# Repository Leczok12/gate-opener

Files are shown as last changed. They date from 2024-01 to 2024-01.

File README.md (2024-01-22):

# GATE OPENER V2

## Description

This device can open gate remotly using ESP RainMaker app or Google home.

## Files

- 3D files (case for remtoe and device)
  - [device](./case/device/)
  - [remote](./case/remote/)
- Kicad files (pcb files)
  - [ready for print pdf files](./pcb/)
  - [device](./pcb/main-board/)
  - [remote](./pcb/remote-controller-board/)
- Arduino IDE files (with software)
  - [software](./software/)

## Appearance of the device

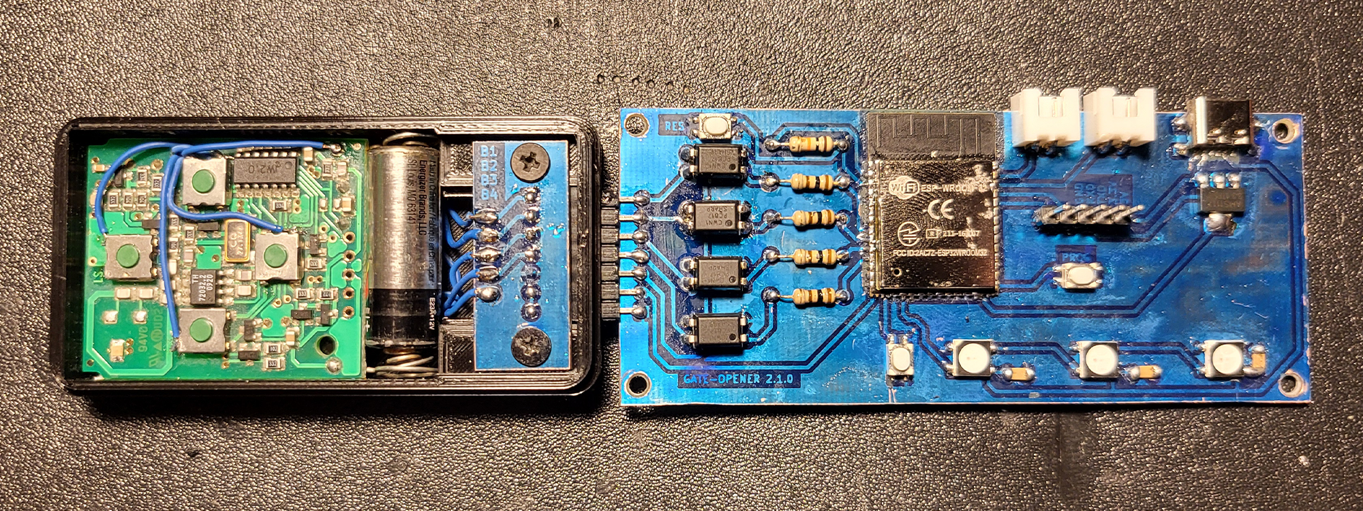
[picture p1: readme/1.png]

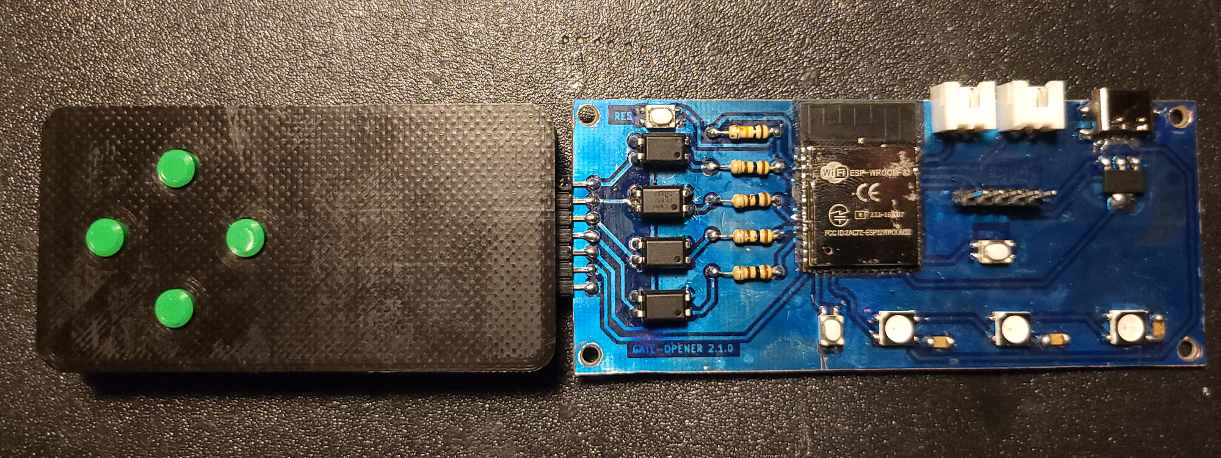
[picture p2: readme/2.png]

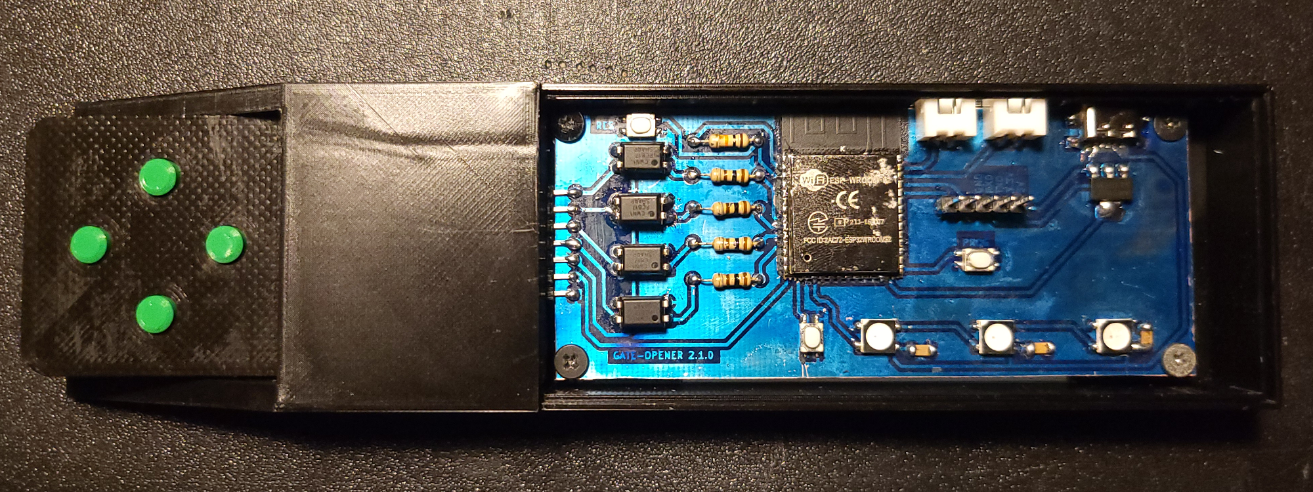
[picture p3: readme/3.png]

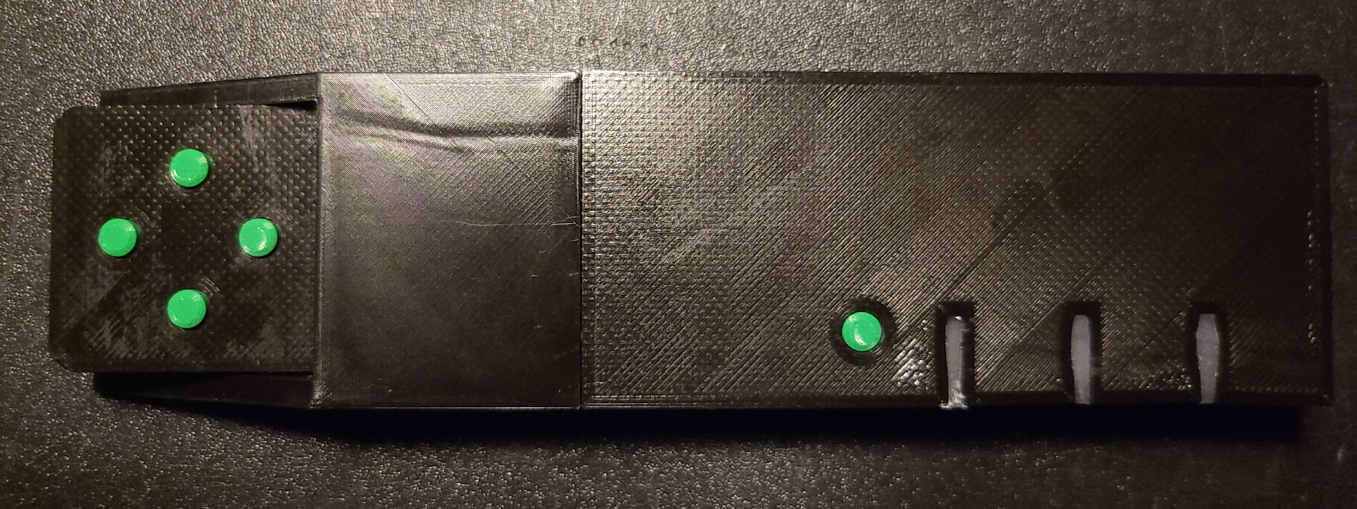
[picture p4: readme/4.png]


## Shopping list

| Name | Amount | Url |
| :---: | :----: | :--- |
| ESP-WROOM32 | 1 | [Aliexpress](https://aliexpress.com/item/32808772590.html) |
| WS2812B LED | 3 | [Aliexpress](https://aliexpress.com/item/4001345875756.html) |
| Capacitor SMD 100nf | 3 | [Aliexpress](https://aliexpress.com/item/1005002769519482.html) |
| USB-C 6 pin | 1 | [Aliexpress](https://aliexpress.com/item/32966491026.html) |
| Pin header 7 pin and 5 pin | 1 | [Aliexpress](https://aliexpress.com/item/1005005258694395.html) |
| Pin socket 7 pin | 1 | [Aliexpress](https://aliexpress.com/item/4001198421663.html) |
| Resistor 10K ohm | 1 | - |
| PC817 | 4 | - |
| Resistor 100ohm | 4 | - |
| Momentary switch 3x4x2.5mm | 3 | - |
| AMS117 3.3V | 1 | - |
| JST_XH_2.54 2 pin sockets  | 2 | - |
| gate remote\* | 1 | - |

\* in my case it is **HORMANN HSM4-868**

## Software

### Requirements

- ARDUINO IDE
  - NeoPixel
  - RainMaker

Create config.hpp file in software dir using config-template.hpp and fill gaps.

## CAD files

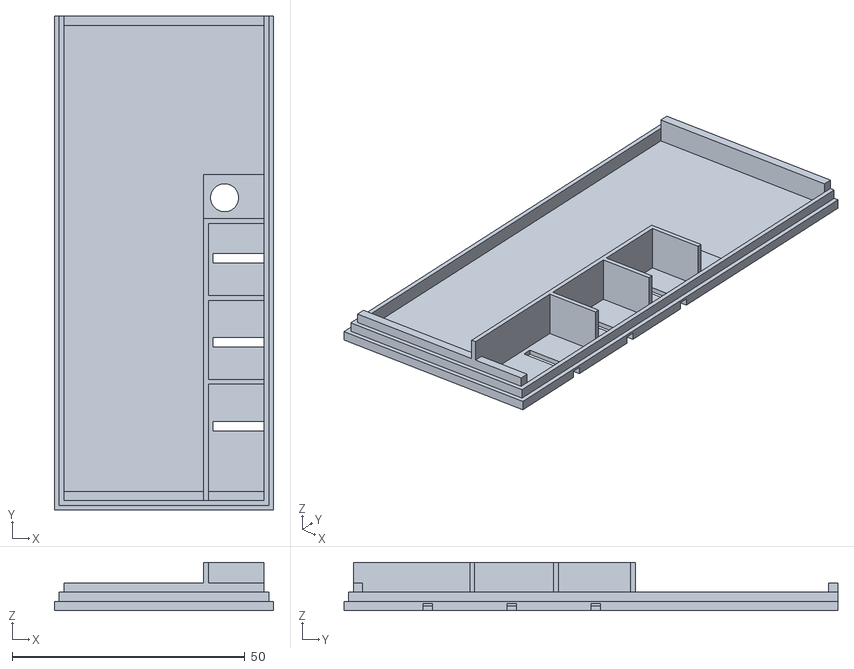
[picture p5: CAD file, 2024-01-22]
case/device/case-top.stl
47.0 x 106.0 x 10.4

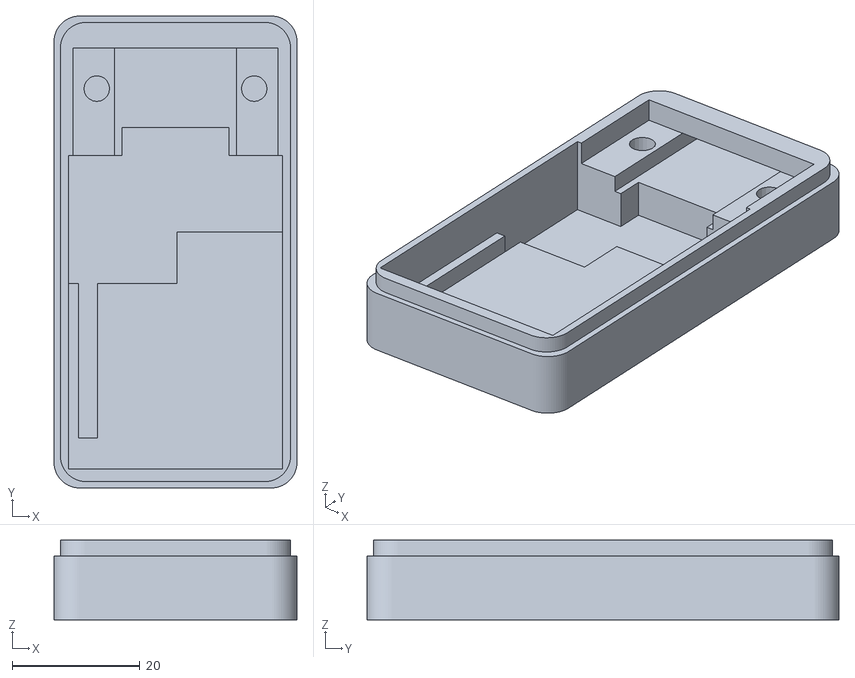
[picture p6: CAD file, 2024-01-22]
case/remote/case-bottom.stl
38.0 x 73.8 x 12.5

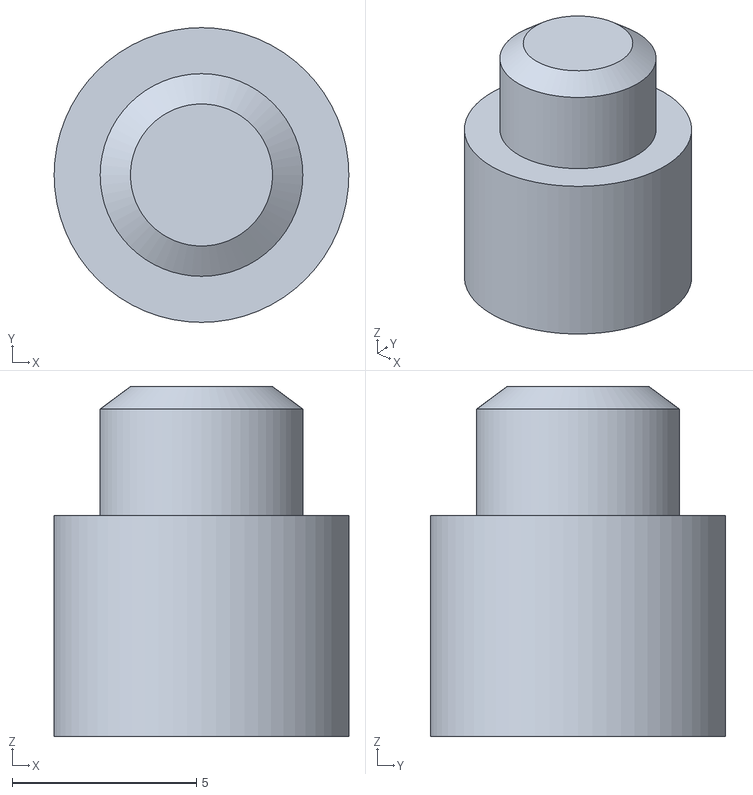
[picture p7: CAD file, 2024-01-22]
case/device/button.stl
8.00 x 8.00 x 9.50

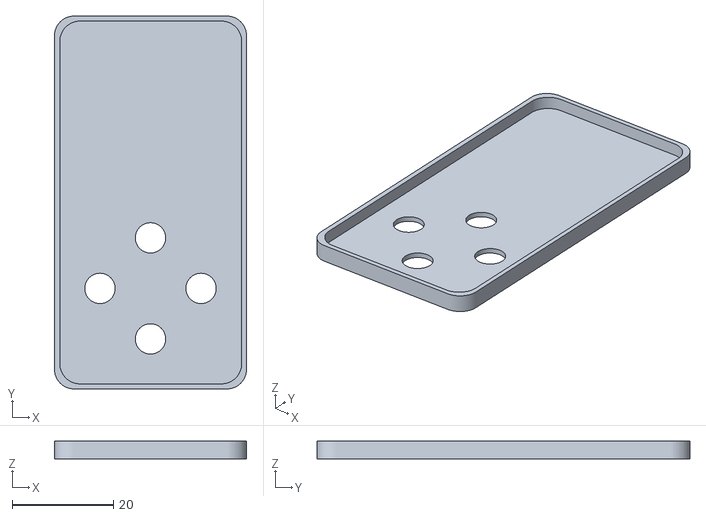
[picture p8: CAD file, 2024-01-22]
case/remote/case-top.stl
38.0 x 73.8 x 3.50

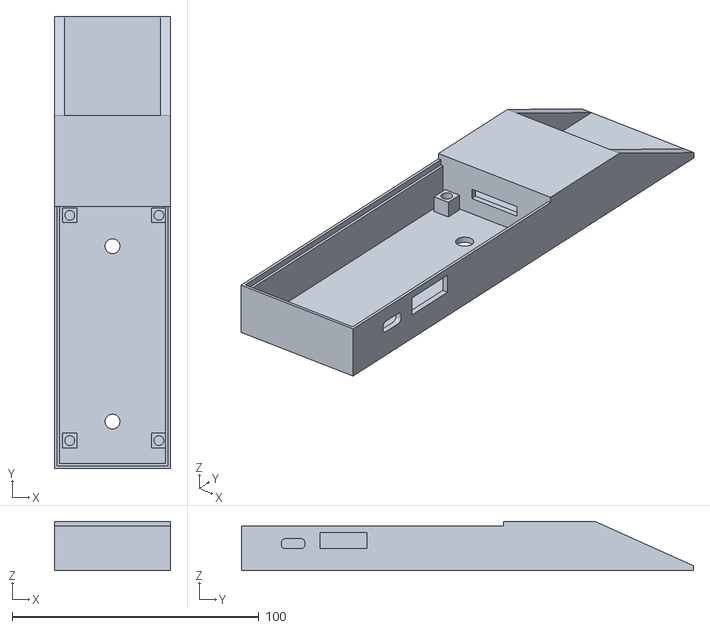
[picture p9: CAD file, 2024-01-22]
case/device/case-bottom.stl
47.0 x 183.0 x 20.0

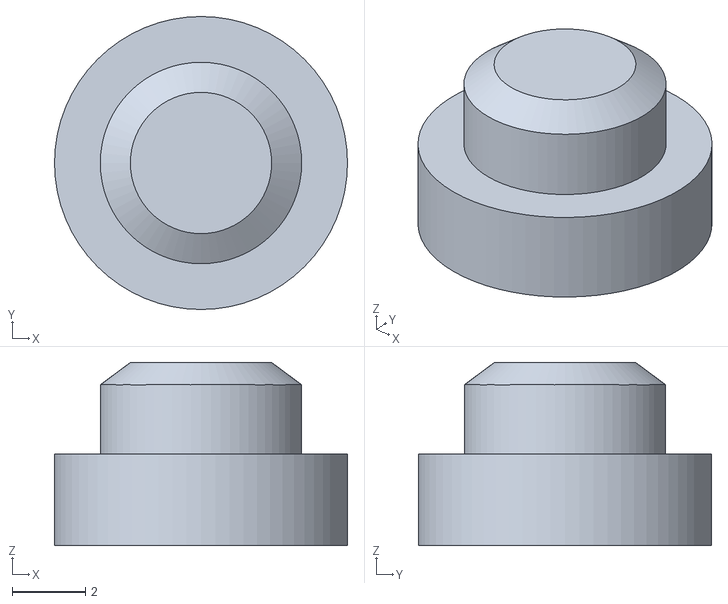
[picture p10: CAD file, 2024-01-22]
case/remote/button.stl
8.00 x 8.00 x 5.00

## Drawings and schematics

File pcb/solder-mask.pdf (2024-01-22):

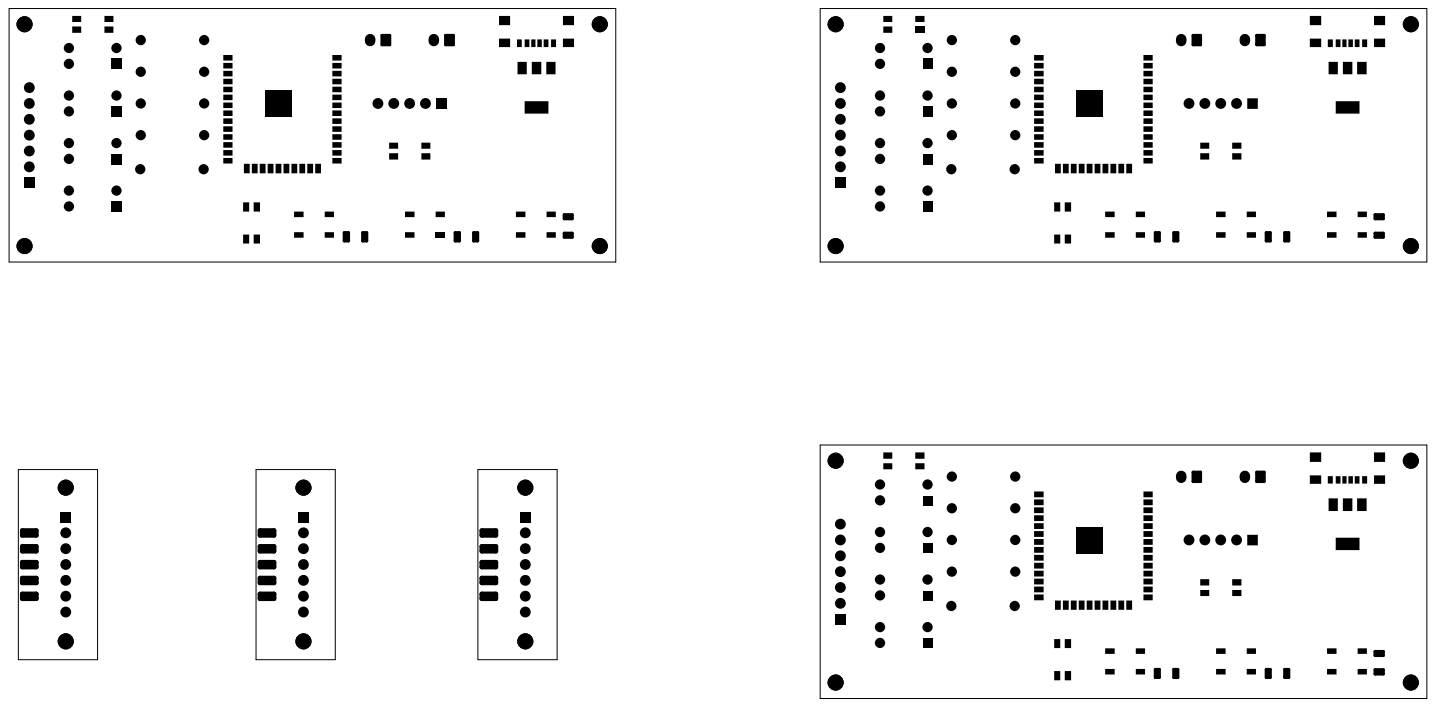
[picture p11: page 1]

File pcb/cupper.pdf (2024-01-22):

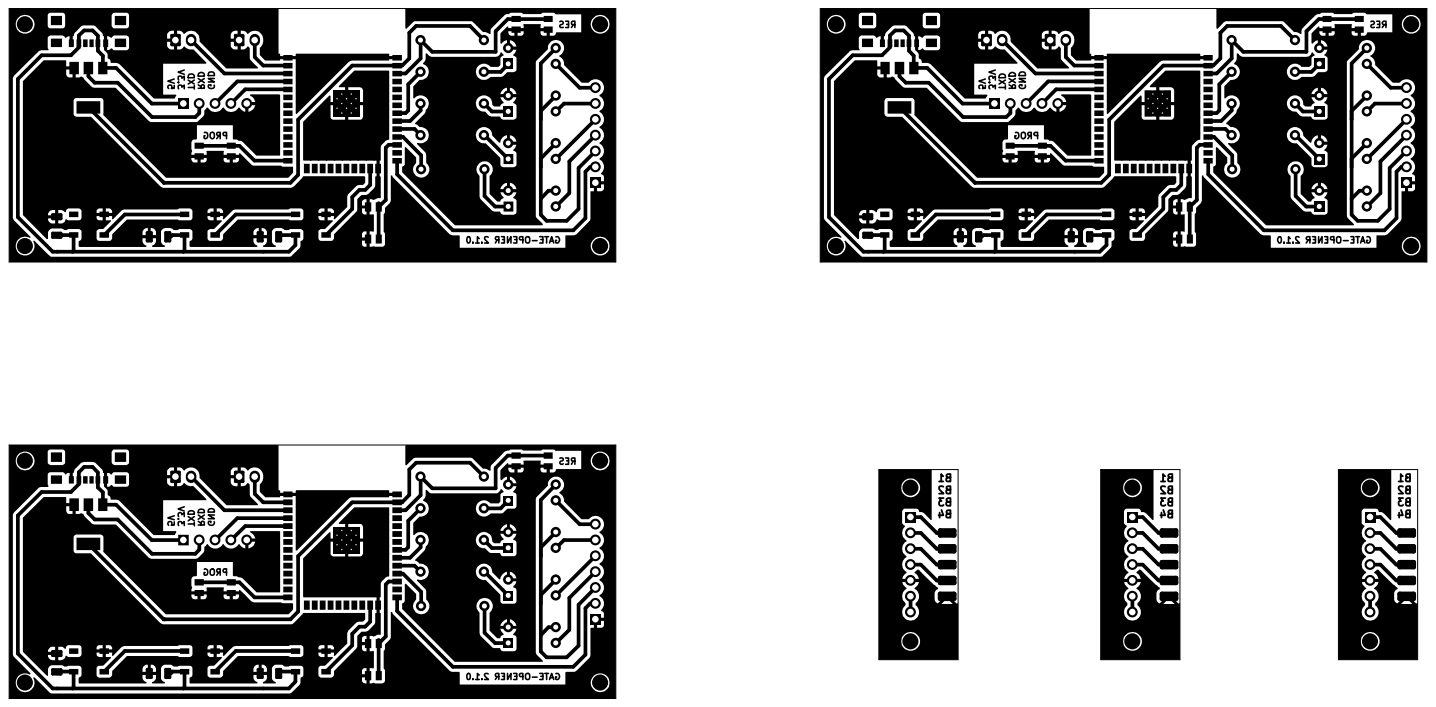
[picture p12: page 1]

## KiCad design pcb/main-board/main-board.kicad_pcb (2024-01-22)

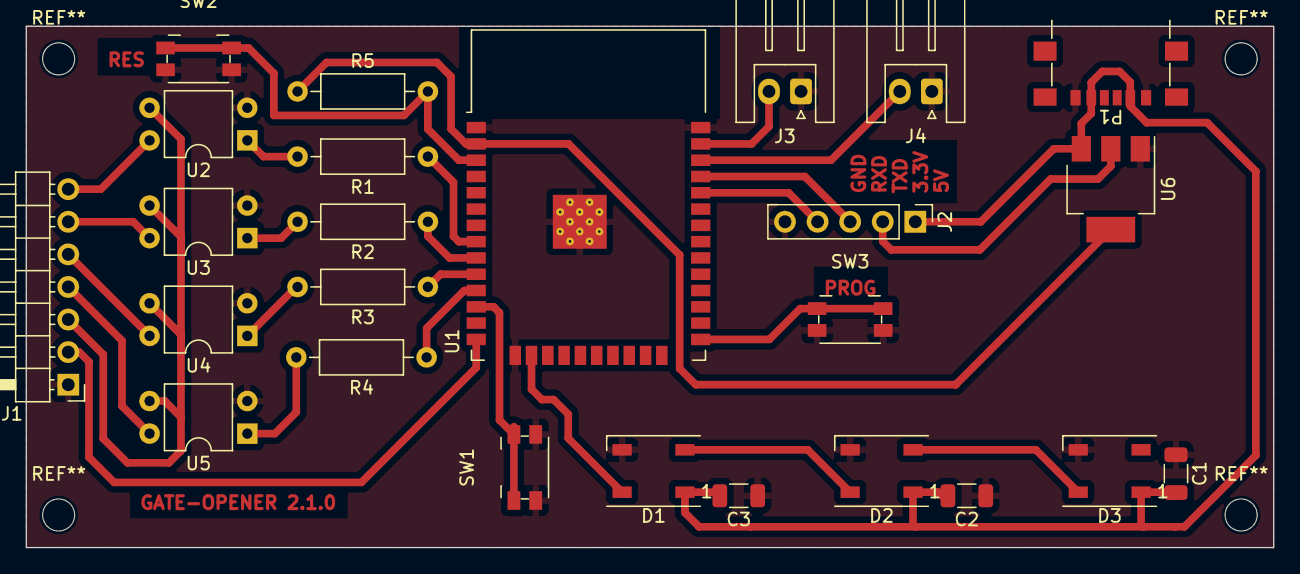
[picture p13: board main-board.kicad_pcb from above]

Board: 2 copper layers, 97.3 x 40.6 mm, 25 parts (0 on the bottom side), 27 nets.

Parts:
C1, C2, C3: 100nF; C_1206_3216Metric
D1, D2, D3: WS2812B; LED_WS2812B_PLCC4_5.0x5.0mm_P3.2mm
J1: Conn_01x07; PinHeader_1x07_P2.54mm_Horizontal
J2: Conn_01x05; PinHeader_1x05_P2.54mm_Vertical
J3, J4: Conn_01x02; JST_XH_S2B-XH-A_1x02_P2.50mm_Horizontal
P1: USB_C_Plug_USB2.0; USB_C_Receptacle_GCT_USB4135-GF-A_6P_TopMnt_Horizontal
R1, R2, R3, R4: 100R; R_Axial_DIN0207_L6.3mm_D2.5mm_P10.16mm_Horizontal
R5: 10k; R_Axial_DIN0207_L6.3mm_D2.5mm_P10.16mm_Horizontal
SW1: SW_Push; Panasonic_EVQPUM_EVQPUD
SW2: RESET; Panasonic_EVQPUM_EVQPUD
SW3: PROG; Panasonic_EVQPUM_EVQPUD
U1: ESP32-WROOM-32
U2, U3, U4, U5: PC817; DIP-4_W7.62mm
U6: AMS1117; SOT-223-3_TabPin2

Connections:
3.3V: J2.2, R5.1, U1.2 (VDD), U6.2 (VO)
5V: C1.2, C2.2, C3.2, D1.1 (VDD), D2.1 (VDD), D3.1 (VDD), J2.1, P1.A9 (VBUS), P1.B9 (VBUS), U6.3 (VI)
EN: R5.2, SW2.1, U1.3 (EN)
GND: C1.1, C2.1, C3.1, D1.3 (VSS), D2.3 (VSS), D3.3 (VSS), J1.1, J2.5, J3.1, J4.1, P1.A12 (GND), P1.B12 (GND), SW1.2, SW2.2, SW3.2, U1.1 (GND), U1.15 (GND), U1.38 (GND), U1.39 (GND), U2.2, U3.2, U4.2, U5.2, U6.1 (ADJ)
GND2: J1.3, U2.3, U3.3, U4.3, U5.3
IO0: SW3.1, U1.25 (IO0)
IO12: J1.2, U1.14 (IO12)
IO13: D1.4 (DIN), U1.16 (IO13)
IO22: J4.2, U1.36 (IO22)
IO23: J3.2, U1.37 (IO23)
IO25: R3.1, U1.10 (IO25)
IO26: R4.1, U1.11 (IO26)
IO27: SW1.1, U1.12 (IO27)
IO32: R1.1, U1.8 (IO32)
IO33: R2.1, U1.9 (IO33)
unnamed: D1.2 (DOUT), D2.4 (DIN)
unnamed: D2.2 (DOUT), D3.4 (DIN)
unnamed: R1.2, U2.1
unnamed: R2.2, U3.1
unnamed: R3.2, U4.1
unnamed: R4.2, U5.1
RE1: J1.7, U2.4
RE2: J1.6, U3.4
RE3: J1.5, U4.4
RE4: J1.4, U5.4
RXD: J2.4, U1.34 (RXD0/IO3)
TXD: J2.3, U1.35 (TXD0/IO1)

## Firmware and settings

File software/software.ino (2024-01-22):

#include <RMaker.h>
#include <WiFi.h>
#include <WiFiProv.h>
#include <AppInsights.h>
#include <Adafruit_NeoPixel.h>

#include "config.hpp"
#include "QuickButton.h"

QuickButton button(GPIO_PIN_BUTTON);
Adafruit_NeoPixel pixels(3, GPIO_PIN_LED, NEO_GRB + NEO_KHZ800);
bool lock = false; // by button
bool remoteConnected = false; // by unplug remote conntroller

struct _Switch{
  Switch * instance;
  bool active;
  unsigned long activeTime;
  int pin;
};

_Switch sw1 = {nullptr, false, 0, GPIO_PIN_SWITCH_1};
_Switch sw2 = {nullptr, false, 0, GPIO_PIN_SWITCH_2};
_Switch sw3 = {nullptr, false, 0, GPIO_PIN_SWITCH_3};
_Switch sw4 = {nullptr, false, 0, GPIO_PIN_SWITCH_4};

// static Switch *sw1 = nullptr; 
// static Switch *sw2 = nullptr; 
// static Switch *sw3 = nullptr; 
// static Switch *sw4 = nullptr; 

// bool sw1_start = false;
// bool sw2_start = false;
// bool sw3_start = false;
// bool sw4_start = false;

// unsigned long sw1_time = 0;
// unsigned long sw2_time = 0;
// unsigned long sw3_time = 0;
// unsigned long sw4_time = 0;

void sysProvEvent(arduino_event_t *sys_event){
  switch (sys_event->event_id) {
    case ARDUINO_EVENT_PROV_START:
        Serial.printf("\nProvisioning Started with name \"%s\" and PoP \"%s\" on BLE\n",SERVICE_NAME, POP);
        printQR(SERVICE_NAME, POP, "ble");
        break;
    case ARDUINO_EVENT_PROV_INIT:
        wifi_prov_mgr_disable_auto_stop(10000);
        break;
    case ARDUINO_EVENT_PROV_CRED_SUCCESS:
        wifi_prov_mgr_stop_provisioning();
        break;
    default:;
  }
};

void switchCallback(Device *device, Param *param, const param_val_t val, void *priv_data, write_ctx_t *ctx){
    const char *device_name = device->getDeviceName();
    const char *param_name = param->getParamName();

    if(strcmp(device_name, "SW_1") == 0){
      sw1.active = (val.val.b ? true : false);
      param->updateAndReport(val);
    }
    else if(strcmp(device_name, "SW_2") == 0){
      sw2.active = (val.val.b ? true : false);
      param->updateAndReport(val);
    }
    else if(strcmp(device_name, "SW_3") == 0){
      sw3.active = (val.val.b ? true : false);
      param->updateAndReport(val);
    }
    else if(strcmp(device_name, "SW_4") == 0){
      sw4.active = (val.val.b ? true : false);
      param->updateAndReport(val);
    };
};

void buttonCallback(unsigned long duration, int count){
  if(duration > 15000){
    Serial.printf("Reset to factory.\n");
    blink(INDEX_LED_POWER);
    RMakerFactoryReset(0);
  }
  else if(duration > 5000){
    Serial.printf("Reset Wi-Fi.\n");
    blink(INDEX_LED_WIFI);
    RMakerWiFiReset(0);
  }
  else if(count == 2){
    lock = !lock;
  }
};

void blink(int pixel){
  auto oldPixel = pixels.getPixelColor(pixel);
  for (int i = 0; i < 5; i++) {
    pixels.setPixelColor(pixel, i%2 == 0 ? 0x000000 : 0xFFFFFF);
    pixels.show();
    delay(300);
  }
  pixels.setPixelColor(pixel,oldPixel);
  pixels.show();
};

bool areSwitchesLow(){
  if(digitalRead(sw1.pin) == LOW && digitalRead(sw2.pin) == LOW && digitalRead(sw3.pin) == LOW && digitalRead(sw4.pin) == LOW)
    return true;
  return false;
};

void switchLoop(_Switch &sw){
  if (areSwitchesLow() && sw.active) {
    sw.active = false;
    if(remoteConnected && !lock){
      sw.activeTime = millis();
      digitalWrite(sw.pin, HIGH);
    }
    else{
      sw.activeTime = 0;
      digitalWrite(sw.pin, LOW);
      sw.instance->updateAndReportParam(ESP_RMAKER_DEF_POWER_NAME, false);
    }
  };

  if(sw.activeTime != 0 && sw.activeTime + VIRTUAL_PRESS_TIME < millis()){
    sw.activeTime = 0;
    digitalWrite(sw.pin, LOW);
    sw.instance->updateAndReportParam(ESP_RMAKER_DEF_POWER_NAME, false);
  };
};

void setup() {
  Serial.begin(115200);

  button.onClick(buttonCallback);

  pinMode(sw1.pin, OUTPUT);
  pinMode(sw2.pin, OUTPUT);
  pinMode(sw3.pin, OUTPUT);
  pinMode(sw4.pin, OUTPUT);
  pinMode(GPIO_PIN_REMOTE_CONNECTED, INPUT_PULLUP);

  Node node;
  node = RMaker.initNode(NODE_NAME);

  sw1.instance = new Switch("SW_1", &GPIO_PIN_SWITCH_1, false);
  sw1.instance->addCb(switchCallback);
  node.addDevice(*sw1.instance);

  sw2.instance = new Switch("SW_2", &GPIO_PIN_SWITCH_2, false);
  sw2.instance->addCb(switchCallback);
  node.addDevice(*sw2.instance);

  sw3.instance = new Switch("SW_3", &GPIO_PIN_SWITCH_3, false);
  sw3.instance->addCb(switchCallback);
  node.addDevice(*sw3.instance);

  sw4.instance = new Switch("SW_4", &GPIO_PIN_SWITCH_4, false);
  sw4.instance->addCb(switchCallback);
  node.addDevice(*sw4.instance);

  RMaker.enableOTA(OTA_USING_TOPICS);
  RMaker.enableTZService();
  RMaker.enableSchedule();
  RMaker.enableScenes();
  initAppInsights();
  RMaker.enableSystemService(SYSTEM_SERV_FLAGS_ALL, 2, 2, 2);
  RMaker.start();
  WiFi.onEvent(sysProvEvent);
  WiFiProv.beginProvision(WIFI_PROV_SCHEME_BLE, WIFI_PROV_SCHEME_HANDLER_FREE_BTDM, WIFI_PROV_SECURITY_1, POP, SERVICE_NAME);

  pixels.begin();
  pixels.clear();
  pixels.show();
};

unsigned long lastBlinkTime = 0;
bool blinkOn = false;

void loop() {
  button.loop();
  digitalRead(GPIO_PIN_REMOTE_CONNECTED) == HIGH ? remoteConnected = false : remoteConnected = true;

  if(lastBlinkTime + BLINK_INTERVAL < millis()){
    //POWER LED
    pixels.setPixelColor(INDEX_LED_POWER,pixels.Color(0,255,0));
    
    //WIFI LED
    pixels.setPixelColor(INDEX_LED_WIFI, (blinkOn && WiFi.isConnected() ? 0xFFAA00 : 0x0));
    
    //WORKING LED
    if(!areSwitchesLow())
      pixels.setPixelColor(INDEX_LED_WORKING, (blinkOn ? 0x0000FF : 0x0));
    else if(lock)
      pixels.setPixelColor(INDEX_LED_WORKING, 0xFF0000);
    else if(!remoteConnected)
      pixels.setPixelColor(INDEX_LED_WORKING, (blinkOn ? 0xFF0000 : 0x0));
    else
      pixels.setPixelColor(INDEX_LED_WORKING, 0x0);

    pixels.setBrightness(60);
    pixels.show();
    lastBlinkTime = millis();
    blinkOn = !blinkOn;
  }

  switchLoop(sw1);
  switchLoop(sw2);
  switchLoop(sw3);
  switchLoop(sw4);
};

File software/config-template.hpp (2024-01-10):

// Variables
constexpr const char *SERVICE_NAME = ""; // REQUIRED
constexpr const char *POP = "";          // REQUIRED

constexpr unsigned long VIRTUAL_PRESS_TIME = 2000; // in miliseconds
constexpr unsigned long BLINK_INTERVAL = 300;      // in miliseconds

constexpr const char *NODE_NAME = "controller";

constexpr int INDEX_LED_POWER = 0;
constexpr int INDEX_LED_WIFI = 1;
constexpr int INDEX_LED_WORKING = 2;

// Pins
constexpr int GPIO_PIN_BUTTON = 27;
constexpr int GPIO_PIN_LED = 13;
constexpr int GPIO_PIN_REMOTE_CONNECTED = 12;

int GPIO_PIN_SWITCH_1 = 32;
int GPIO_PIN_SWITCH_2 = 33;
int GPIO_PIN_SWITCH_3 = 25;
int GPIO_PIN_SWITCH_4 = 26;

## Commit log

2023-10-15 update device
2023-11-02 update case & pcb, fix connection
    [gate-opener-body-bottom.stl, gate-opener-piston.stl, gate-opener-servo-holder.stl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]
2024-01-10 last changes for version 1
    [pcb.kicad_pcb]
2024-01-10 init main-v2
    [gate-opener-body-bottom.stl, gate-opener-piston.stl, gate-opener-servo-holder.stl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]
2024-01-10 quick fix
    [main-board.kicad_pcb, main-board.kicad_sch, remote-controller-board.kicad_pcb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]
2024-01-22 New PCB & case
    [bottom.stl, button.stl, case-bottom.stl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]
